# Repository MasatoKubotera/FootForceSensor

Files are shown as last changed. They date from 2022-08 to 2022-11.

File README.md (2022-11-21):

<html lang="en">
  <head>
    <meta charset="uft-8">
    <meta name="author" content="Masato Kubotera">
  </head>
  <body>
    <h1>FootForceSensor Ver. 1.0</h1>
    <h2>About FootForceSensor</h2>
    <p>
      FootForceSensor is a sensor that measures the pressure applied to the sole of a biped robot's foot by attaching strain gauges (load cells) to four locations on each foot.<br>
      It is under development to detect the position of the robot's center of gravity and to improve gait control.
      <h3>About Ver. 1.0</h3>
      The values of the four strain gages can be read by the Pro Micro (usable as an Aruduino Leonardo) and transferred to the computer board via a USB interface or a 3.3V system RS-485 interface to which Kondo's B3M servo motors can be connected.<br>
      Power can be supplied from the same connector as one communication, from USB bus power in the case of USB interface communication, or from Kondo's B3M servo motor connector in the case of RS-485 interface communication.<br>
      To allow left and right legs to use the same firmware, a shortland is grounded on the board to identify left and right.
      <table>
        <tr>
          <td>
            <a href="image/brd_top.png">
              <div align="center">
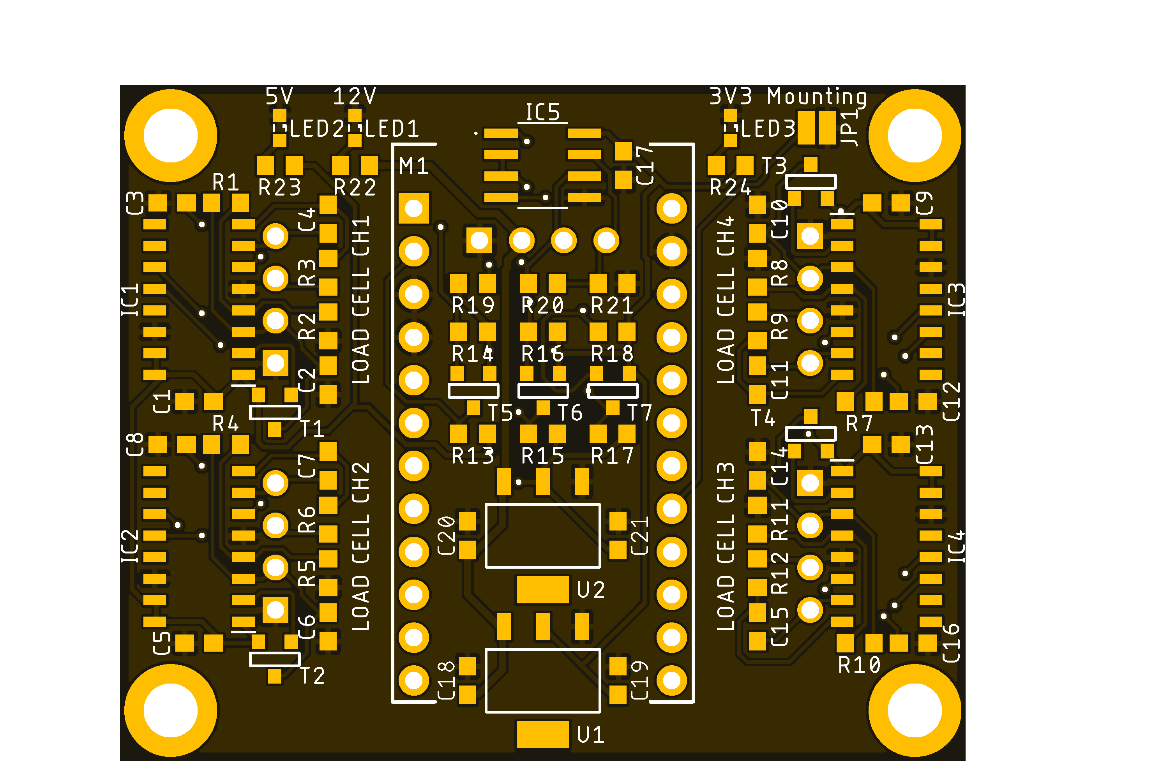
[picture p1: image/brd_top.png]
                
              </div>
            </a>
          </td>
          <td>
            <div align="center">
              under construction<br>
              
            </div>
          </td>
        </tr>
        <tr>
          <td>
            <div align="center">
              PCB preview image
            </div>
          </td>
          <td>
            <div align="center">
              After component mounting
            </div>
          </td>    
        </tr>
      </table>
    </p>
    <h2>Repository Contents</h2>
    <p>
    <dl>
      <dt>\image</dt>
      <dd>PCB preview images and capture of design screen</dd>
      <dt>\libraries</dt>
      <dd>Libraries used in Autodesk Eagle design</dd>
      <dt>Schematic.pdf</dt>
      <dd>Circuit diagram of this product</dd>
      <dt>BOM.txt</dt>
      <dd>Parts lists output from design data</dd>
      <dt>.brd</dt>
      <dd>Board wiring design file by Autodesk Eagle</dd>
      <dt>.sch</dt>
      <dd>Schematic design file by Autodesk Eagle</dd>
      <dt>Gerber_data.zip</dt>
      <dd>Zip folder of Gerber format files for PCB manufacturing requests.</dd>
      <dt>LICENSE</dt>
      <dd>This is a license to use this product. Please confirm before use.</dd>
      <dt>.gitignore</dt>
      <dd>File to exclude cache files from management.</dd>
    </dl>
    </p>
    <h2>Documentation</h2>
      <p>
        <h3>BOM</h3>
          <table>
            <thead>
              <tr>
                <th> Eagle Design Parts # </th>
                <th> Q'ty </th>
                <th> Mfr. Product # </th>
                <th> Supplier </th>
                <th> Description </th>
              </tr>
            </thead>
            <tbody>
              <tr>
                <td> C1, C2, C3, C5, C6, C8, C9, C10, C12, C13, C14, C16 </td>
                <td> 12 </td>
                <td> GRM188R71E105KA12 </td>
                <td> <a href="https://akizukidenshi.com/catalog/g/gP-14526/">Akizuki</a> </td>
                <td> Multilayer Ceramic Capacitors SMD/SMT 1uF 25V 10% 0603 </td>
              </tr>
              <tr>
                <td> C18, C19, C20, C21 </td>
                <td> 4 </td>
                <td> GRM188R6YA106MA73 </td>
                <td> <a href="https://akizukidenshi.com/catalog/g/gP-13161/">Akizuki</a> </td>
                <td> Multilayer Ceramic Capacitors SMD/SMT 10uF 35V 20% 0603 </td>
              </tr>
              <tr>
                <td> C4, C7, C11, C15, C17 </td>
                <td> 5 </td>
                <td> GCM188L81H104K57 </td>
                <td> <a href="https://akizukidenshi.com/catalog/g/gP-16143/">Akizuki</a> </td>
                <td> Multilayer Ceramic Capacitors SMD/SMT 0.1uF 50V 10% 0603 </td>
              </tr>
              <tr>
                <td> CH1, CH2, CH3, CH4, CH5 </td>
                <td> 5 </td>
                <td> S4B-XH-A(LF)(SN) </td>
                <td> <a href="https://akizukidenshi.com/catalog/g/gC-12842/">Akizuki</a> </td>
                <td> Connector Header Through Hole, Right Angle 4 position 2.5mm </td>
              </tr>
              <tr>
                <td> IC1, IC2, IC3, IC4 </td>
                <td> 4 </td>
                <td> HX711 </td>
                <td> <a href="https://akizukidenshi.com/catalog/g/gI-12473/">Akizuki</a> </td>
                <td> 24-Bit Analog-to-Digital Converter (ADC) for Weigh Scales </td>
              </tr>
              <tr>
                <td> IC5 </td>
                <td> 1 </td>
                <td> ADM3078E </td>
                <td> <a href="https://www.mouser.jp/ProductDetail/584-ADM3078EARZ">Mouser</a> </td>
                <td> RS-485/RS-422 Transceiver (Half Duplex, 16 Mbps, DE/RE) </td>
              </tr>
              <tr>
                <td> LED1, LED2, LED3 </td>
                <td> 3 </td>
                <td> 150060VS86000 </td>
                <td> <a href="https://www.mouser.jp/ProductDetail/710-150060VS86000">Mouser</a> </td>
                <td> Standard LEDs - SMD Green 2V 20mA 573nm 0603 </td>
              </tr>
              <tr>
                <td> M1 </td>
                <td> 1 </td>
                <td> DEV-12640 </td>
                <td> <a href="https://www.mouser.jp/ProductDetail/474-DEV-12640">Mouser</a> </td>
                <td> Development Boards & Kits - AVR Pro Micro - 5V/16MHz </td>
              </tr>
              <tr>
                <td> M1 </td>
                <td> 1 </td>
                <td> 6604S-40 </td>
                <td> <a href="https://akizukidenshi.com/catalog/g/gP-01591/">Akizuki</a> </td>
                <td> 2.54mm Pin Socket Strip, Single Row </td>
              </tr>
              <tr>
                <td> M1 </td>
                <td> 1 </td>
                <td> PHA-1x40SG </td>
                <td> <a href="https://akizukidenshi.com/catalog/g/gC-06631/">Akizuki</a> </td>
                <td> 2.54mm Pin Header Strip, Straight, Single Row </td>
              </tr>
              <tr>
                <td> R1, R4, R7, R10 </td>
                <td> 4 </td>
                <td> RC0603FR-1320KL </td>
                <td> <a href="https://www.mouser.jp/ProductDetail/603-RC0603FR-1320KL">Mouser</a> </td>
                <td> Thick Film Resistors - SMD 20 kOhms 100-200mW 1% 0603 </td>
              </tr>
              <tr>
                <td> R13, R14, R15, R16, R17, R18 </td>
                <td> 6 </td>
                <td> RC0603FR-1010KL </td>
                <td> <a href="https://www.mouser.jp/ProductDetail/603-RC0603FR-1010KL">Mouser</a> </td>
                <td> Thick Film Resistors - SMD 10 kOhms 100-200mW 1% 0603 </td>
              </tr>
              <tr>
                <td> R19, R21 </td>
                <td> 2 </td>
                <td> RC0603FR-10680RL </td>
                <td> <a href="https://www.mouser.jp/ProductDetail/603-RC0603FR-10680RL">Mouser</a> </td>
                <td> Thick Film Resistors - SMD 680 Ohms 100-200mW 1% 0603 </td>
              </tr>
              <tr>
                <td> R2, R5, R8, R11 </td>
                <td> 4 </td>
                <td> RC0603FR-138K2L </td>
                <td> <a href="https://www.mouser.jp/ProductDetail/603-RC0603FR-138K2L">Mouser</a> </td>
                <td> Thick Film Resistors - SMD 8.2 kOhms 100-200mW 1% 0603 </td>
              </tr>
              <tr>
                <td> R20 </td>
                <td> 1 </td>
                <td> RC0603FR-10120RL </td>
                <td> <a href="https://www.mouser.jp/ProductDetail/603-RC0603FR-10120RL">Mouser</a> </td>
                <td> Thick Film Resistors - SMD 120 Ohms 100-200mW 1% 0603 </td>
              </tr>
              <tr>
                <td> R3, R6, R9, R12, R22, R23, R24 </td>
                <td> 7 </td>
                <td> RC0603FR-101KL </td>
                <td> <a href="https://www.mouser.jp/ProductDetail/603-RC0603FR-101KL">Mouser</a> </td>
                <td> Thick Film Resistors - SMD 1 kOhms 100-200mW 1% 0603 </td>
              </tr>
              <tr>
                <td> T1, T2, T3, T4 </td>
                <td> 4 </td>
                <td> MMBT3906 </td>
                <td> <a href="https://akizukidenshi.com/catalog/g/gI-05967/">Akizuki</a> </td>
                <td> Bipolar Transistors - BJT Bipolar Transistor, SOT-23, 40V, 200mA, PNP </td>
              </tr>
              <tr>
                <td> T5, T6, T7 </td>
                <td> 3 </td>
                <td> BSS138 </td>
                <td> <a href="https://akizukidenshi.com/catalog/g/gI-04232/">Akizuki</a> </td>
                <td> 50V N-Channel Enhancement Mode MOSFET - ESD Protected </td>
              </tr>
              <tr>
                <td> U1 </td>
                <td> 1 </td>
                <td> LM1117GS-3.3 </td>
                <td> <a href="https://akizukidenshi.com/catalog/g/gI-16989/">Akizuki</a> </td>
                <td> LDO Voltage Regulator 3.3V 1A </td>
              </tr>
              <tr>
                <td> U2 </td>
                <td> 1 </td>
                <td> LD1117S50 </td>
                <td> <a href="https://akizukidenshi.com/catalog/g/gI-15255/">Akizuki</a> </td>
                <td> LDO Voltage Regulator 5.0V 0.8A </td>
              </tr>
            </tbody>
          </table>          
        <h3>PCB Fabrication</h3>
          PCB(Printed Circuit Board) manufacturing was outsourced to <a href="https://www.elecrow.com/pcb-manufacturing.html">Elecrow</a>.<br>
          The custom specifications are as follows.
          <ul>
            <li>Layer : 2 layers</li>
            <li>Dimensions : 50 x 40</li>
            <li>Different PCB Design : 1eg</li>
            <li>PCB Thickness : 1.6</li>
            <li>PCB Color : Black</li>
            <li>Surface Finish : HASL</li>
            <li>Castellated Hole : No</li>
            <li>Copper Weight : 1oz</li>
            <li>PCB Stencil : Stencil 10cm X 10cm no frame[Top]</li>
          </ul>
          The data used to order fabrication are as follows.
          <ul>
            <li>Eagle design rule : <a href="https://www.elecrow.com/download/Elecrow_PCB_eagle_rule.zip">Elecrow Eagle Design Rule</a></li>
            <li>Eagle CAM file : <a href="https://www.elecrow.com/download/Elecrow_Gerber_Generater_DrillAlign.zip">Elecrow CAM file</a></li>
            <li>Gerber format data : <a href="/Gerber_data.zip">Gerber_data.zip</a></li>
          </ul>
      </p>
    <h2>Contact</h2>
    <p>
    If you have any questions, please contact MasatoKubotera, the product's designer, by E-mail.<br>
    E-mail : <a href="mailto:masatokubotera06@yahoo.co.jp">masatokubotera06@yahoo.co.jp</a>
    </p>
    <h2>License Information</h2>
    <p>
      This product is open source.<br>
      Please review the <a href="/LICENSE">LICENSE file</a> for license information.<br>
      <br>
      <strong>FootForceSensor Ver. 1.0</strong> by Masato Kubotera is licensed under a <a href="http://creativecommons.org/licenses/by-nc-sa/4.0/">Creative Commons Attribution-NonCommercial-ShareAlike 4.0 International License</a>.
    </p>    
  </body>
</html>

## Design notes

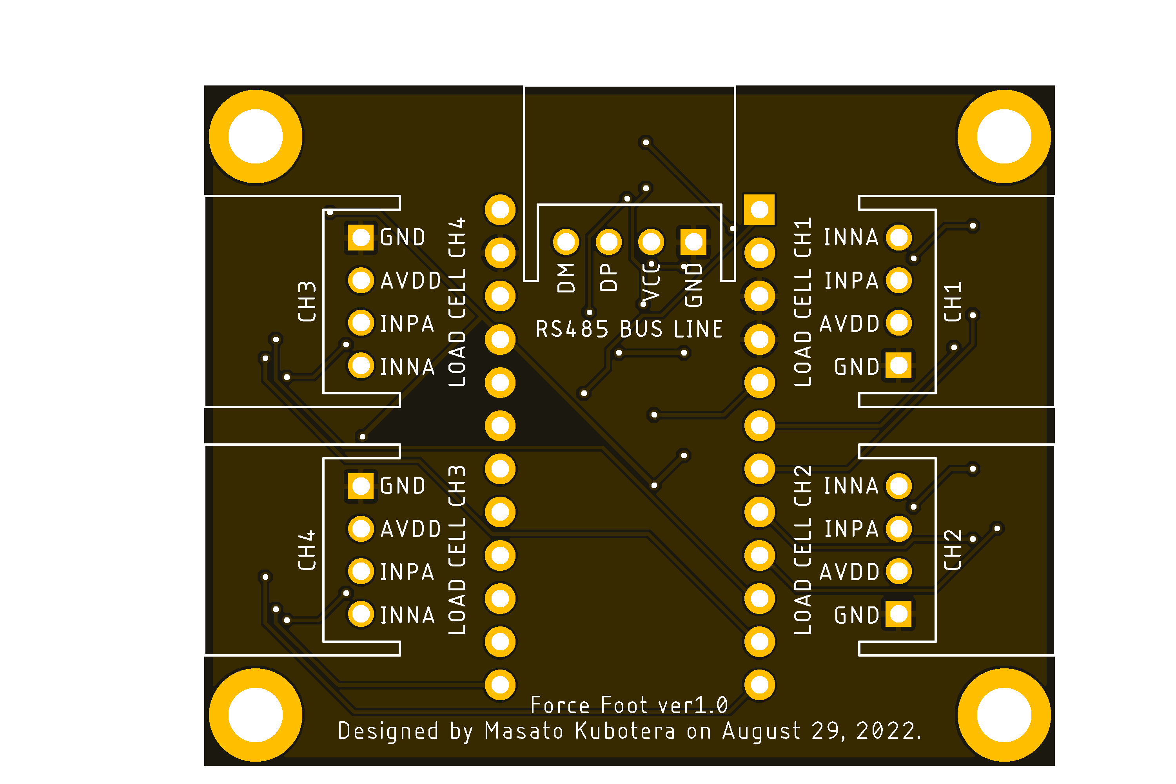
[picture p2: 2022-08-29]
image/brd_bottom.png

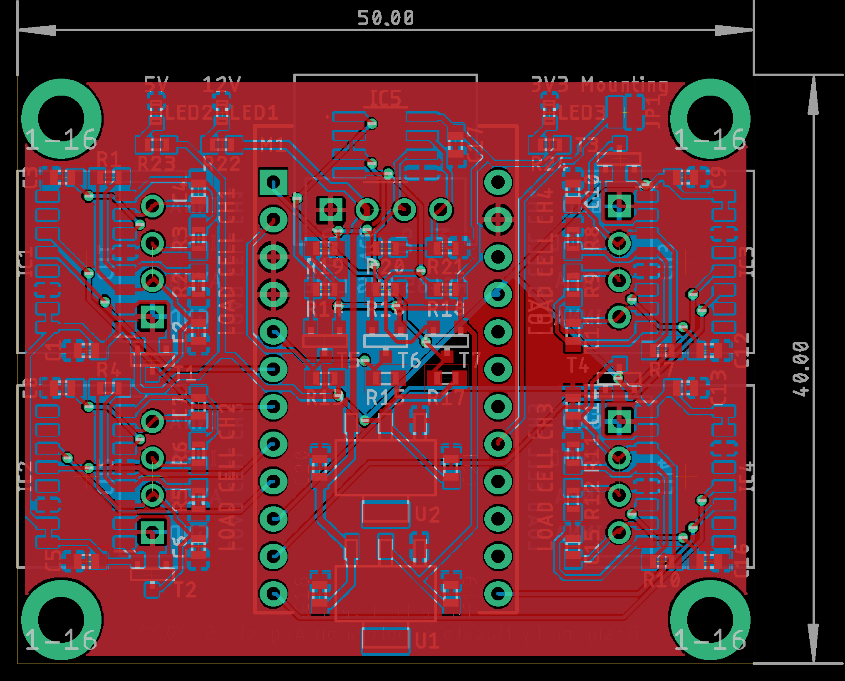
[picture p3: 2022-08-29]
image/brd.png

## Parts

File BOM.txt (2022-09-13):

Partlist exported from C:/Users/Masato/Documents/citbrains/FootForceSensor/FootForceSensor_ver1_0.sch at 2022/09/08 15:05

Qty Value                  Device                 Package                Parts                                               Description                
3                          LEDSML0603             SML0603                LED1, LED2, LED3                                    LED                        
5   0.1u                   C-USC0603              C0603                  C4, C7, C11, C15, C17                               CAPACITOR, American symbol 
6   10k                    R-US_R0603             R0603                  R13, R14, R15, R16, R17, R18                        RESISTOR, American symbol  
4   10u                    C-USC0603              C0603                  C18, C19, C20, C21                                  CAPACITOR, American symbol 
1   120                    R-US_R0603             R0603                  R20                                                 RESISTOR, American symbol  
7   1k                     R-US_R0603             R0603                  R3, R6, R9, R12, R22, R23, R24                      RESISTOR, American symbol  
12  1u                     C-USC0603              C0603                  C1, C2, C3, C5, C6, C8, C9, C10, C12, C13, C14, C16 CAPACITOR, American symbol 
4   20k                    R-US_R0603             R0603                  R1, R4, R7, R10                                     RESISTOR, American symbol  
2   680                    R-US_R0603             R0603                  R19, R21                                            RESISTOR, American symbol  
4   8.2k                   R-US_R0603             R0603                  R2, R5, R8, R11                                     RESISTOR, American symbol  
1   ADM3078E               ADM3078E               ADM3078E               IC5                                                                            
3   BSS138                 BSS138                 BSS138                 T5, T6, T7                                                                     
4   HX711                  HX711                  HX711                  IC1, IC2, IC3, IC4                                                             
1   LD1117S50              LD1117S50              SOT-223                U2                                                                             
1   LM1117GS-3.3           LM1117GS-3.3           SOT-223                U1                                                                             
4   MMBT3906               PNPSOT23               SOT-23                 T1, T2, T3, T4                                      PNP TRANSISTOR             
1   PRO_MICRO_THROUGH_HOLE PRO_MICRO_THROUGH_HOLE PRO_MICRO_THROUGH_HOLE M1                                                                             
5   S4B-XH-A               S4B-XH-A               S4B-XH-A               CH1, CH2, CH3, CH4, CH5                                                        
1   SHORTLAND              SHORTLAND              SHORTLAND              JP1

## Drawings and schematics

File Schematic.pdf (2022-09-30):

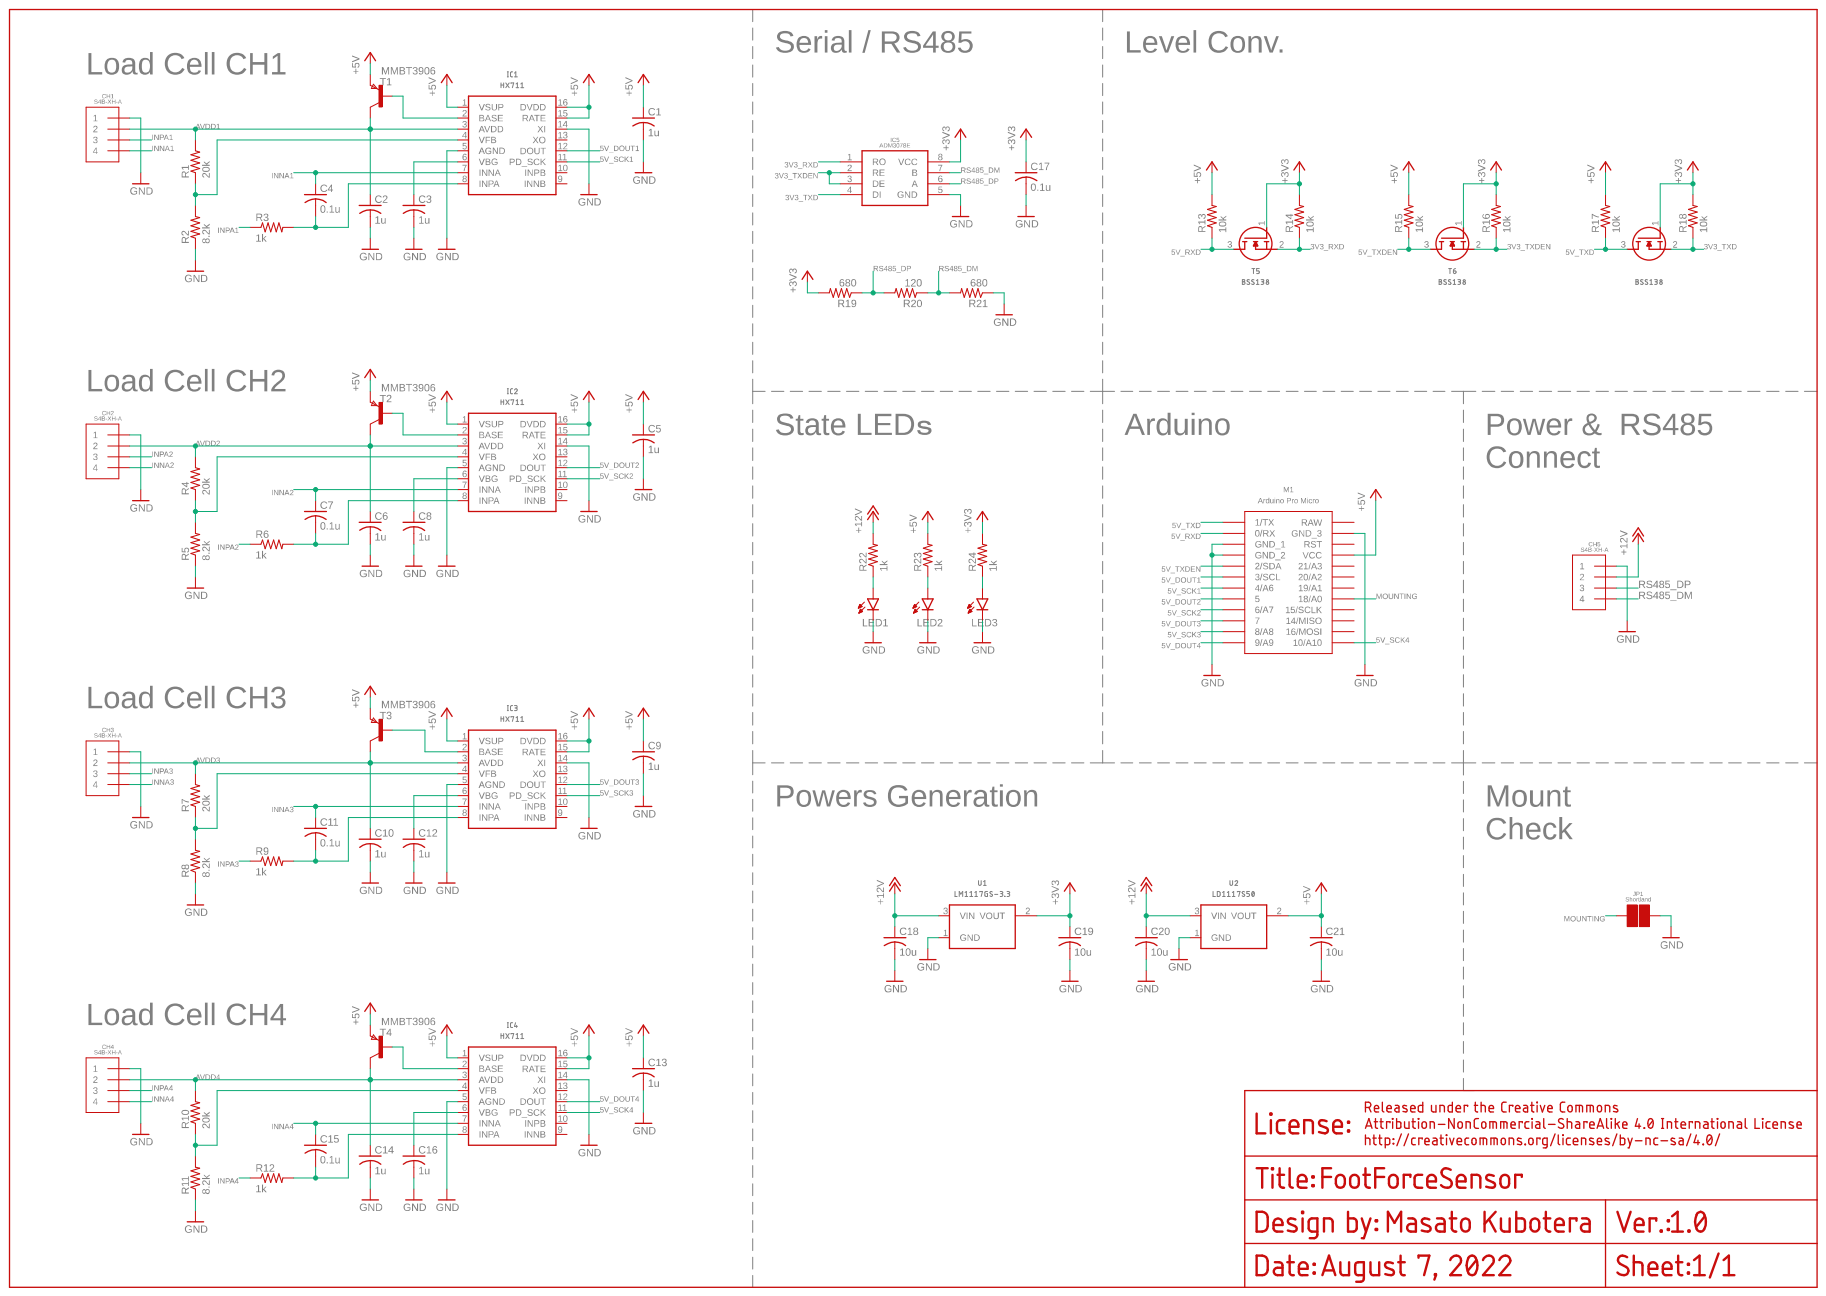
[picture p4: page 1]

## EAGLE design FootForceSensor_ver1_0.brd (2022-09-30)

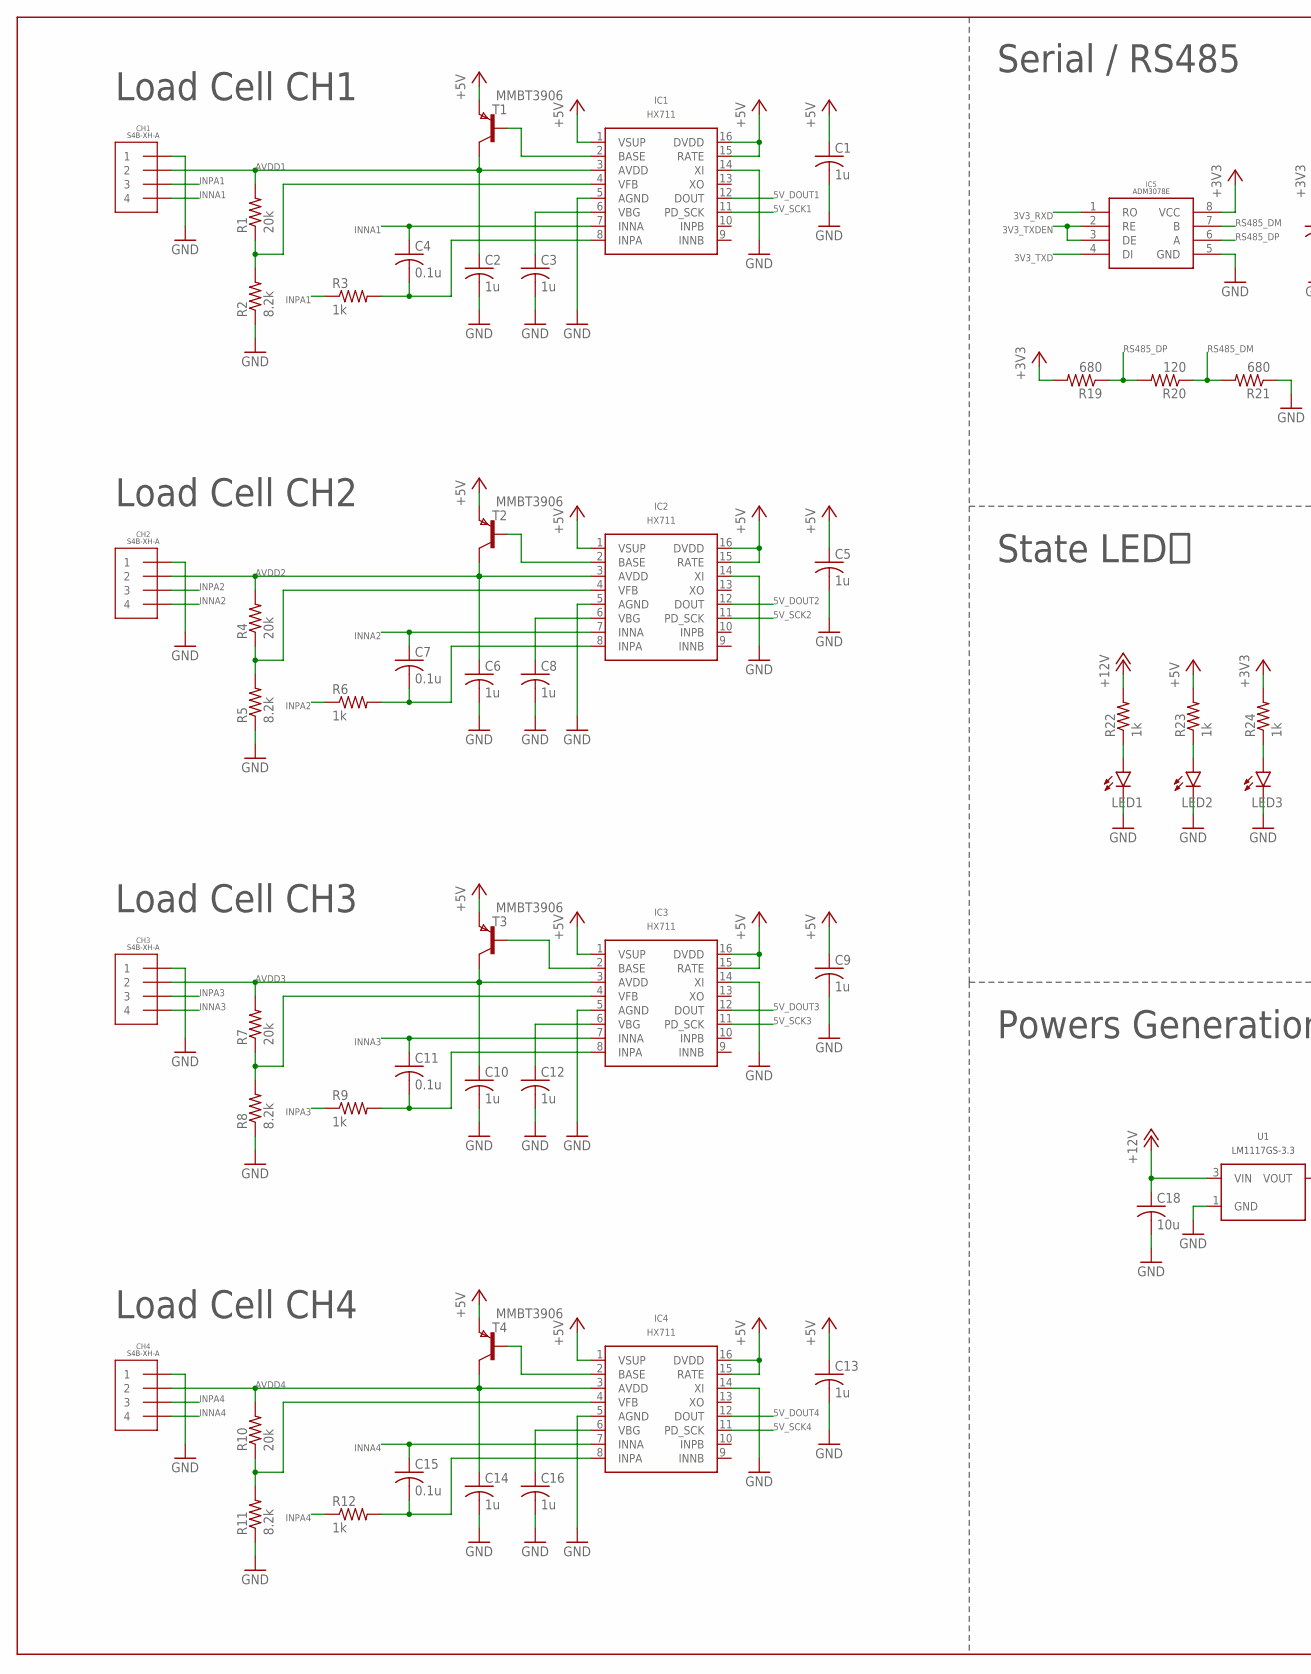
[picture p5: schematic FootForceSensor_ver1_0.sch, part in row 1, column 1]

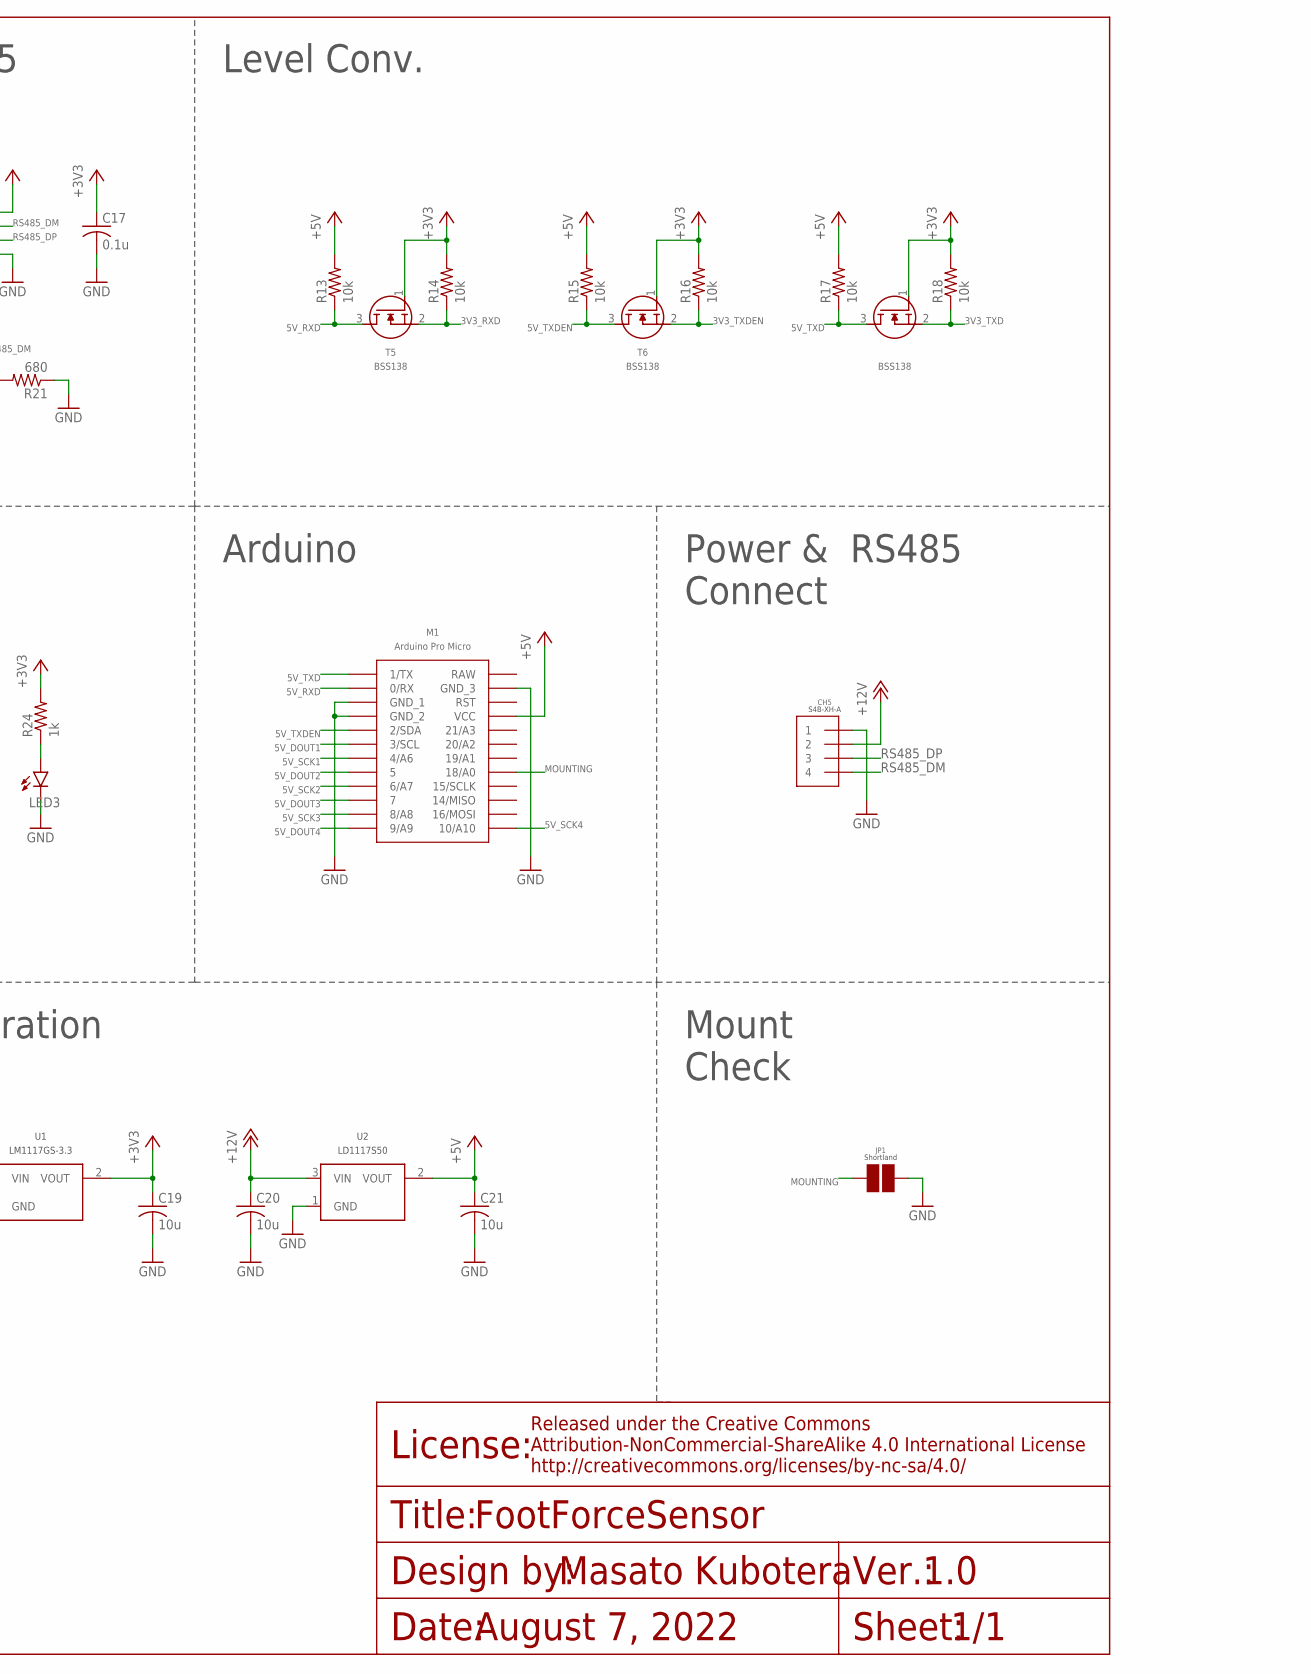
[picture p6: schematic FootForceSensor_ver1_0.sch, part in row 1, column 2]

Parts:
C1, C2, C3, C5, C6, C8, C9, C10, C12, C13, C14, C16: 1u; C0603
C4, C7, C11, C15, C17: 0.1u; C0603
C18, C19, C20, C21: 10u; C0603
CH1, CH2, CH3, CH4, CH5: S4B-XH-A
IC1, IC2, IC3, IC4: HX711
IC5: ADM3078E
JP1: SHORTLAND
LED1, LED2, LED3: LEDSML0603; SML0603
M1: PRO_MICRO_THROUGH_HOLE
R1, R4, R7, R10: 20k; R0603
R2, R5, R8, R11: 8.2k; R0603
R3, R6, R9, R12, R22, R23, R24: 1k; R0603
R13, R14, R15, R16, R17, R18: 10k; R0603
R19, R21: 680; R0603
R20: 120; R0603
T1, T2, T3, T4: MMBT3906; SOT-23
T5, T6, T7: BSS138
U1: LM1117GS-3.3; SOT-223
U2: LD1117S50; SOT-223

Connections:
3V3_LED: LED3.A, R24.1
3V3_RXD: IC5.1 (RO), R14.1, T5.2 (S)
3V3_TXD: IC5.4 (DI), R18.1, T7.2 (S)
3V3_TXDEN: IC5.2 (RE), IC5.3 (DE), R16.1, T6.2 (S)
5V_DOUT1: IC1.12 (DOUT), M1.3/SCL
5V_DOUT2: IC2.12 (DOUT), M1.5
5V_DOUT3: IC3.12 (DOUT), M1.7
5V_DOUT4: IC4.12 (DOUT), M1.9/A9
5V_LED: LED2.A, R23.1
5V_RXD: M1.0/RX, R13.1, T5.3 (D)
5V_SCK1: IC1.11 (PD_SCK), M1.4/A6
5V_SCK2: IC2.11 (PD_SCK), M1.6/A7
5V_SCK3: IC3.11 (PD_SCK), M1.8/A8
5V_SCK4: IC4.11 (PD_SCK), M1.10/A10
5V_TXD: M1.1/TX, R17.1, T7.3 (D)
5V_TXDEN: M1.2/SDA, R15.1, T6.3 (D)
12V_LED: LED1.A, R22.1
+3V3: C17.1, C19.1, IC5.8 (VCC), R14.2, R16.2, R18.2, R19.2, R24.2, T5.1 (G), T6.1 (G), T7.1 (G), U1.2 (VOUT)
+5V: C1.1, C5.1, C9.1, C13.1, C21.1, IC1.1 (VSUP), IC1.15 (RATE), IC1.16 (DVDD), IC2.1 (VSUP), IC2.15 (RATE), IC2.16 (DVDD), IC3.1 (VSUP), IC3.15 (RATE), IC3.16 (DVDD), IC4.1 (VSUP), IC4.15 (RATE), IC4.16 (DVDD), M1.VCC, R13.2, R15.2, R17.2, R23.2, T1.2 (E), T2.2 (E), T3.2 (E), T4.2 (E), U2.2 (VOUT)
+12V: C18.1, C20.1, CH5.2, R22.2, U1.3 (VIN), U2.3 (VIN)
AVDD1: C2.1, CH1.2, IC1.3 (AVDD), R1.2, T1.1 (C)
AVDD2: C6.1, CH2.2, IC2.3 (AVDD), R4.2, T2.1 (C)
AVDD3: C10.1, CH3.2, IC3.3 (AVDD), R7.2, T3.1 (C)
AVDD4: C14.1, CH4.2, IC4.3 (AVDD), R10.2, T4.1 (C)
BASE1: IC1.2 (BASE), T1.3 (B)
BASE2: IC2.2 (BASE), T2.3 (B)
BASE3: IC3.2 (BASE), T3.3 (B)
BASE4: IC4.2 (BASE), T4.3 (B)
GND: C1.2, C2.2, C3.2, C5.2, C6.2, C8.2, C9.2, C10.2, C12.2, C13.2, C14.2, C16.2, C17.2, C18.2, C19.2, C20.2, C21.2, CH1.1, CH2.1, CH3.1, CH4.1, CH5.1, IC1.5 (AGND), IC1.14 (XI), IC2.5 (AGND), IC2.14 (XI), IC3.5 (AGND), IC3.14 (XI), IC4.5 (AGND), IC4.14 (XI), IC5.5 (GND), JP1.2, LED1.C, LED2.C, LED3.C, M1.GND_1, M1.GND_2, M1.GND_3, R2.1, R5.1, R8.1, R11.1, R21.1, U1.1 (GND), U2.1 (GND)
INNA1: C4.1, CH1.4, IC1.7 (INNA)
INNA2: C7.1, CH2.4, IC2.7 (INNA)
INNA3: C11.1, CH3.4, IC3.7 (INNA)
INNA4: C15.1, CH4.4, IC4.7 (INNA)
INPA1: CH1.3, R3.1
INPA1_: C4.2, IC1.8 (INPA), R3.2
INPA2: CH2.3, R6.1
INPA2_: C7.2, IC2.8 (INPA), R6.2
INPA3: CH3.3, R9.1
INPA3_: C11.2, IC3.8 (INPA), R9.2
INPA4: CH4.3, R12.1
INPA_: C15.2, IC4.8 (INPA), R12.2
MOUNTING: JP1.1, M1.18/A0
RS485_DM: CH5.4, IC5.7 (B), R20.1, R21.2
RS485_DP: CH5.3, IC5.6 (A), R19.1, R20.2
VBG1: C3.1, IC1.6 (VBG)
VBG2: C8.1, IC2.6 (VBG)
VBG3: C12.1, IC3.6 (VBG)
VBG4: C16.1, IC4.6 (VBG)
VFB1: IC1.4 (VFB), R1.1, R2.2
VFB2: IC2.4 (VFB), R4.1, R5.2
VFB3: IC3.4 (VFB), R7.1, R8.2
VFB4: IC4.4 (VFB), R10.1, R11.2

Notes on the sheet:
Load Cell CH1
Load Cell CH2
Load Cell CH3
Load Cell CH4
Serial / RS485
Powers Generation
Arduino
Level Conv.
State LEDｓ
Power & RS485 Connect
Mount Check
1.0
1/1
August 7, 2022
FootForceSensor

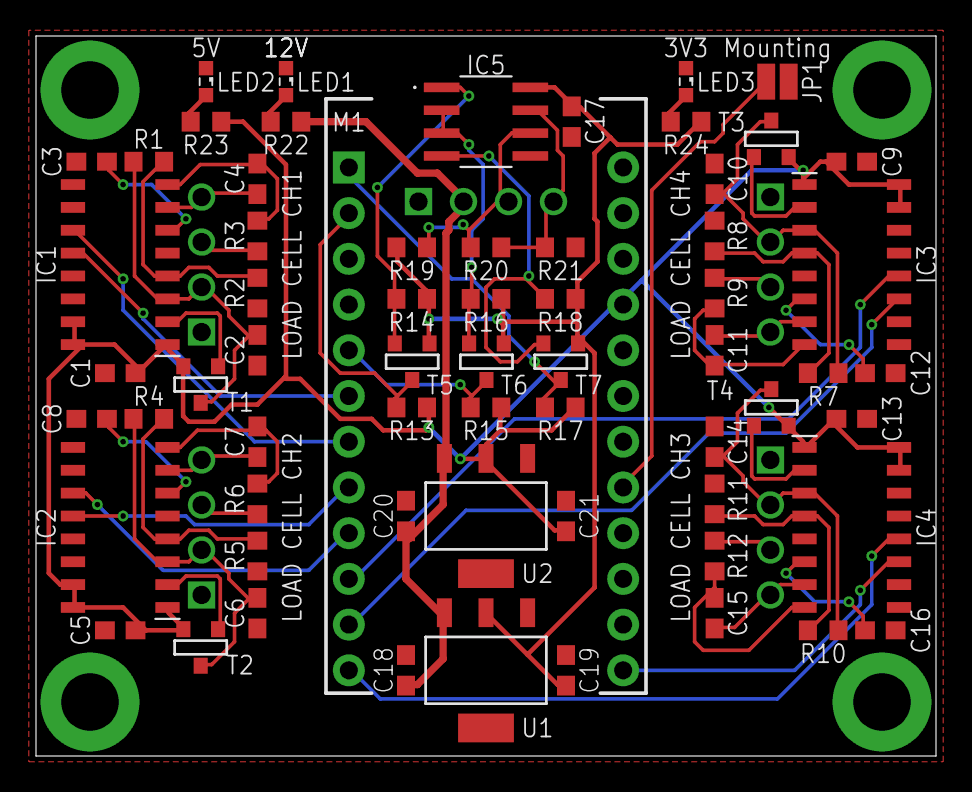
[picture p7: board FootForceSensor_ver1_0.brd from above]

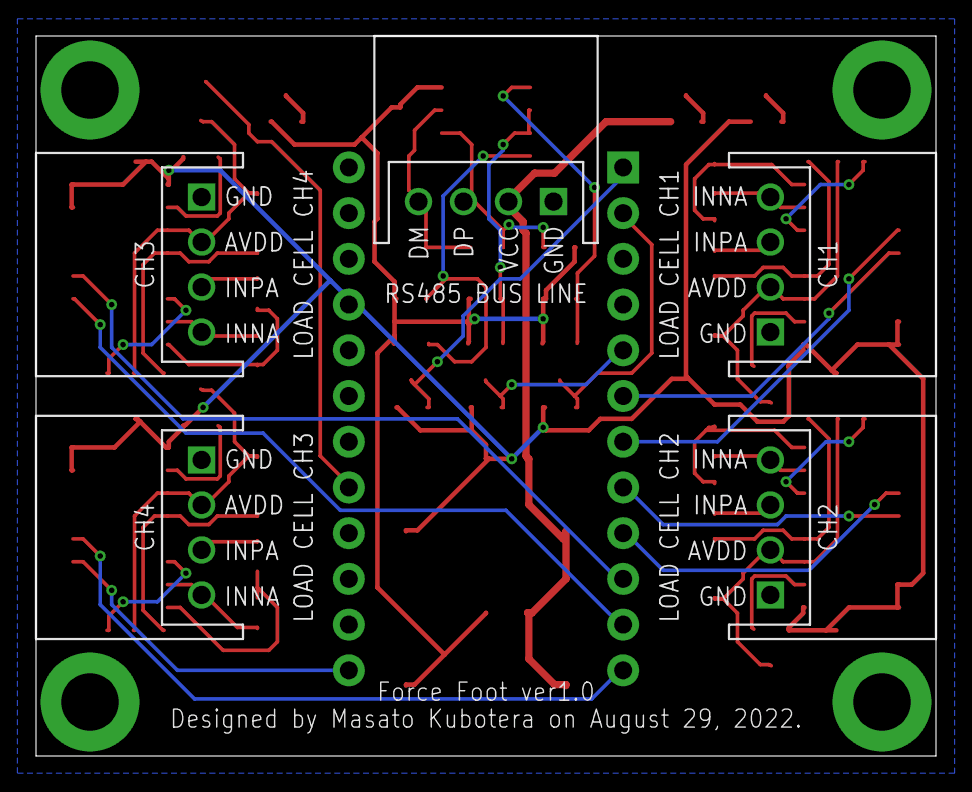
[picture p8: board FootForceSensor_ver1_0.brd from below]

Board: 2 copper layers, 50.0 x 40.0 mm, 69 parts (5 on the bottom side), 52 nets.

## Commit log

2022-08-28 Create a prototype board
    [FootForceSensor_ver1_0.brd, FootForceSensor_ver1_0.sch]
2022-08-29 Create Ordering Version
    [FootForceSensor_ver1_0.brd]
2022-09-13 add BOM
2022-09-30 Maintenance of README and other public information
    [FootForceSensor_ver1_0.brd, FootForceSensor_ver1_0.sch]

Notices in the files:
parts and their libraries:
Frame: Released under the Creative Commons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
